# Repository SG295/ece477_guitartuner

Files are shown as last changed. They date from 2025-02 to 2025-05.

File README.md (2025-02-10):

# Automatic Guitar Tuner 🎸
☆ **Automatic Guitar Tuner Project for ECE477 (Senior Design) @ Purdue University** ☆

**Team Page: https://engineering.purdue.edu/477grp11/Team/team.html**

**Project Description:** Our automatic guitar tuner is a tool anyone can use by selecting the desired note and holding the tool against the tuning peg. A microphone will listen as the string is plucked by the user and make the proper adjustments thorugh a motor. An LCD screen will communicate when the guitar adjustments are finished being made. The design will also have other modes such as a free spin mode to allow the motor to assist in the restringing of a guitar.
Design parameters are:
  * A 3D printed case that holds all the components (PCB, battery, motor, etc.)
  * An STM32 microcontroller that controls all the components of the tuner (battery, motor, LCD screen, microphone)
  * A stepper motor connected to the microcontroller that rotates based on feedback from the microphone
  * A digital microphone that listens when prompted by the microcontroller. First, I2S is used to read the digital signal and then DSP is performed so that the microcontroller knows what frequency is being played.
  * A rechargable battery connected to a battery management system and the microcontroller. Powers all the components in the tuner.
  * A graphical LCD screen that is controlled by buttons on the tuner. It includes "Power", "^", ">", "<", and "v" buttons for the user to press to control the contents of the screen.

***

**For team members:**

Please make a branch for your respective part and title it according (i.e. if you're working on the motor, you can just title it "motor").

The command to create a branch (do this locally after you've pulled):
  * git checkout -b NEW_BRANCH_NAME

The commands (in order) to push your NEW branch: 
  * git add .
  * git commit -m "put message here"
  * git push origin -u NEW_BRANCH_NAME
   
**Once you have created and pushed the branch, you can push normally if you're on the branch. You can check this with "git branch".**

I have setup a platoform IO project here with basic settings with the STM32F407VG Discovery Boards we have at our table (looks like the image below). Make sure you're actually within the project folder (titled "PlatformIO-GuitarTuner") and not this repo when trying to upload code to the board. I'll list some documentation that will be useful below:
  * Reference Manual: https://www.st.com/resource/en/reference_manual/dm00031020-stm32f405-415-stm32f407-417-stm32f427-437-and-stm32f429-439-advanced-arm-based-32-bit-mcus-stmicroelectron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
  * STM32F407 Data Sheet: https://www.st.com/resource/en/datasheet/dm00037051.pdf

**DISCOVERY BOARD:**
71fB+DA9BdL _AC_UF894,1000_QL80_

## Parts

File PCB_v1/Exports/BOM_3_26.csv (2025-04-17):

Reference | Value | MFP | Qty | DNP | Packed?
C2 | 1uF |  | 1
C4 | 0.47uF |  | 1
C8 | 0.01uF |  | 1
C10 | 100uF | EEE1AA101WR | 1
C12 | 0.1uF |  | 1
C25 | 1uF | TAJA105K016RNJ | 1
F1 | C1F 2 | C1F 2 (CA0612KRX7R7BB104) | 1
F2 | MFU0805FF01000P500 | MFU0805FF01000P500 | 1
J3 | JST_B2B-PH-K-S | S2B-PH-K-SLFSN | 1
J6 | OLED Conn_02x04 | Genereic 2x4 2.56 mm | 1
J7 | B4B-XH-A | B4B-XH-A | 1
J8 | Conn_01x02_Pin |  | 1
J9 | Conn_02x05_Odd_Even |  | 1
J10 | Conn_01x03 | Genereic 3 pin 2.56mm | 1
J11 | 1051640001 | 1051640001 | 1
R8 | 0.01 1% | WSL0805R0100FEA1 | 1
R12 | 1.1k |  | 1
R13 | 47k |  | 1
R14 | 1.5k |  | 1
R23 | 10k |  | 1 | DNP
R24 | 47k |  | 1 | DNP
RN1 | 1k | EXB-2HV102JV | 1
RN2 | 10k | EXB-2HV103JV | 1
RN3 | 680 | EXB-38V681JV | 1
RV1 | 10k | TRIM_TC33X-2-103E | 1
SW1 | SW_SPST | JST_B2B-PH-K-S | 1
SW8 | SW_Push | TS04-66-65-BK-160-SMT | 1
SW9 | SW_SPDT | PCM12SMTR | 1
U1 | BQ25185DLHR | BQ25185DLHR | 1
U2 | BQ27441-G1 | BQ27441-G1 | 1
U5 | DRV8834PWP | DRV8834PWP | 1
U6 | MAX7375AXR805 |  | 1
U7 | STM32F405RGTx | STM32F405RGT6 | 1
U8 | ESD9B5.0ST5G | ESD9B5.0ST5G | 1
C6,C7 | 100nF | CA0612KRX7R7BB104 | 2
C11,C17 | 10uF |  | 2
D1,D7 | Orange |  | 2
D9,D10 | Blue |  | 2
J1,J2 | B6B-PH-K-S | B6B-PH-K-S | 2
J4,J5 | Conn_01x05_Pin | Genereic 5 pin 2.56mm | 2
R5,R21 | 1k |  | 2
R15,R16 | 51k |  | 2
R18,R19 | 0.1 | WSTM0805QLR100FNR | 2
U3,U4 | SMS05T1G | SMS05T1G | 2
C1,C3,C5 | 22uF |  | 3
C9,C21,C23 | 2.2uF |  | 3
D2,D3,D6 | Green |  | 3
D4,D5,D8 | Red |  | 3
R6,R7,R11 | 5.1k |  | 3
R1,R2,R3,R4 | 680 |  | 4
TP3,TP4,TP5,TP6 | TestPoint | N/A | 4
R9,R10,R17,R20,R22 | 10k |  | 5
SW2,SW3,SW4,SW5,SW6,SW7 | SW_Push | JST_B2B-PH-K-S | 6
C15,C16,C18,C19,C20,C22,C24 | 100nF |  | 7
TP1,TP8,TP9,TP10,TP11,TP12,TP13 | ~ | N/A | 7

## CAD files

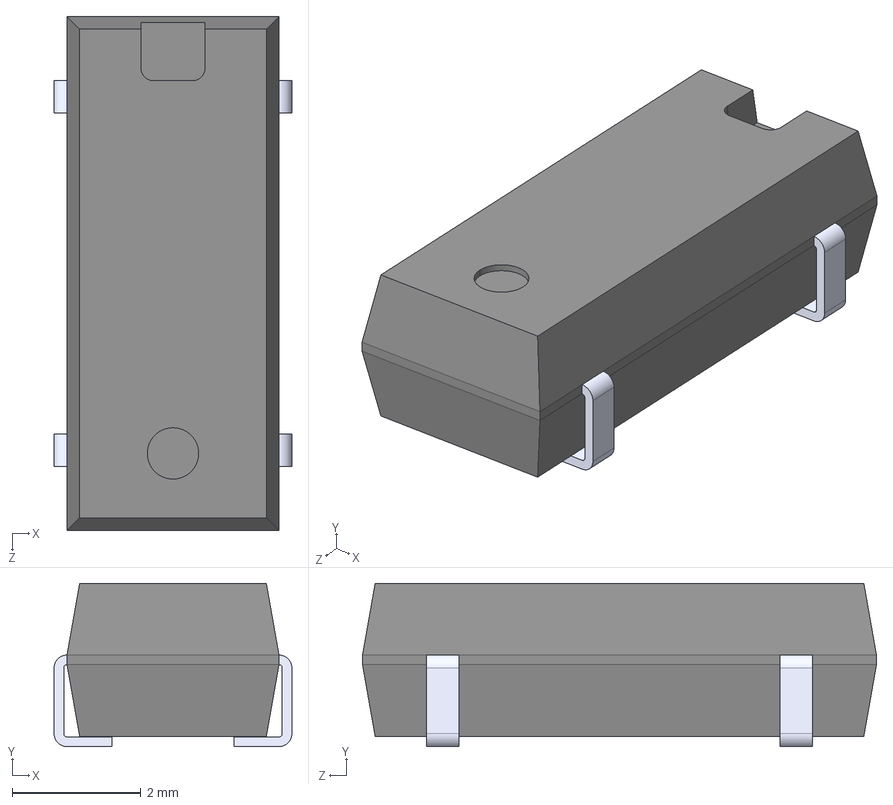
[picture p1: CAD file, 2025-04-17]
Parts_Library/MC-306_32.7680K-A5__ROHS.step
3.70 x 2.54 x 8.00 mm

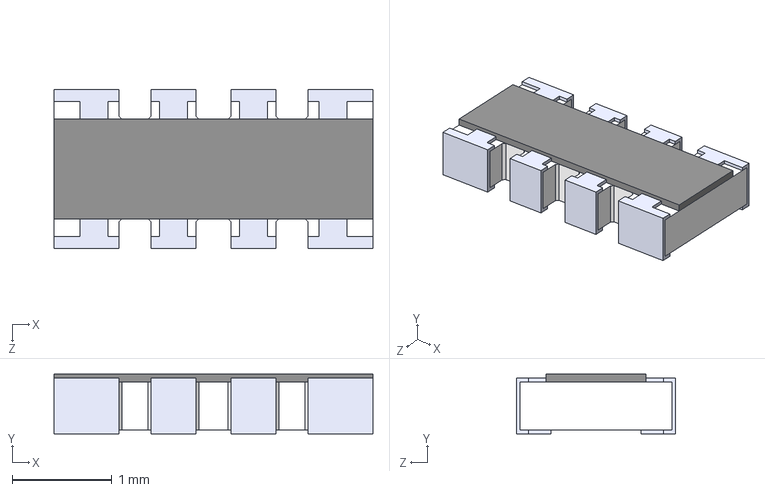
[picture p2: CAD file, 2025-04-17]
Parts_Library/EXB-38V681JV.step
3.20 x 0.6 x 1.60 mm

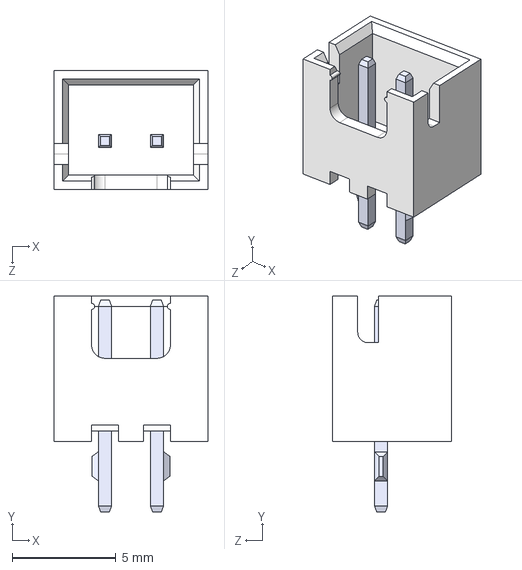
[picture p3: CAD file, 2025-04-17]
Parts_Library/B2B-XH-A.step
7.40 x 10.4 x 5.75 mm

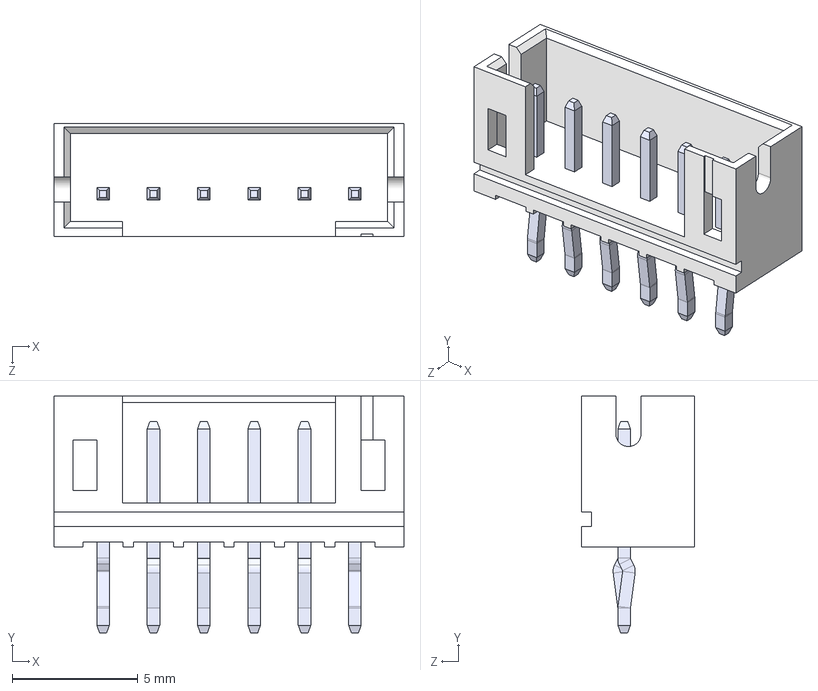
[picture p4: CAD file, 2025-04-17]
Parts_Library/B6B-PH-K-S.step
13.9 x 9.40 x 4.50 mm
pin x 6

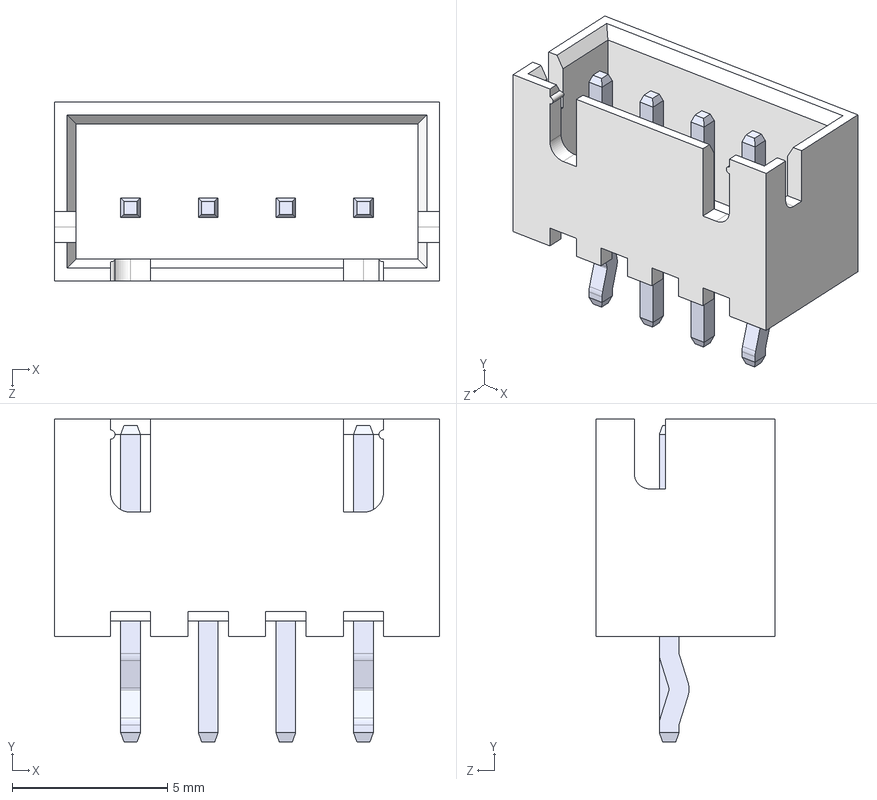
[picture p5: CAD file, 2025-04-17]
Parts_Library/B4B-XH-A.step
12.4 x 10.4 x 5.75 mm

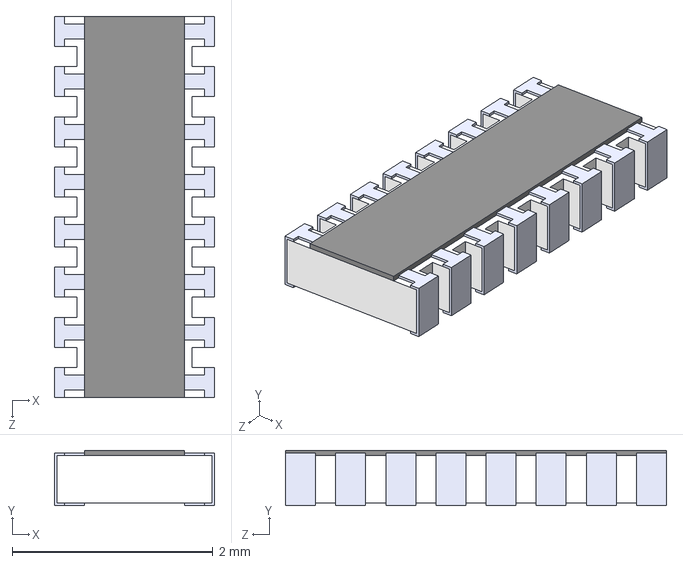
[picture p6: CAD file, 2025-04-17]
Parts_Library/EXB-2HV102JV.step
1.60 x 0.55 x 3.80 mm

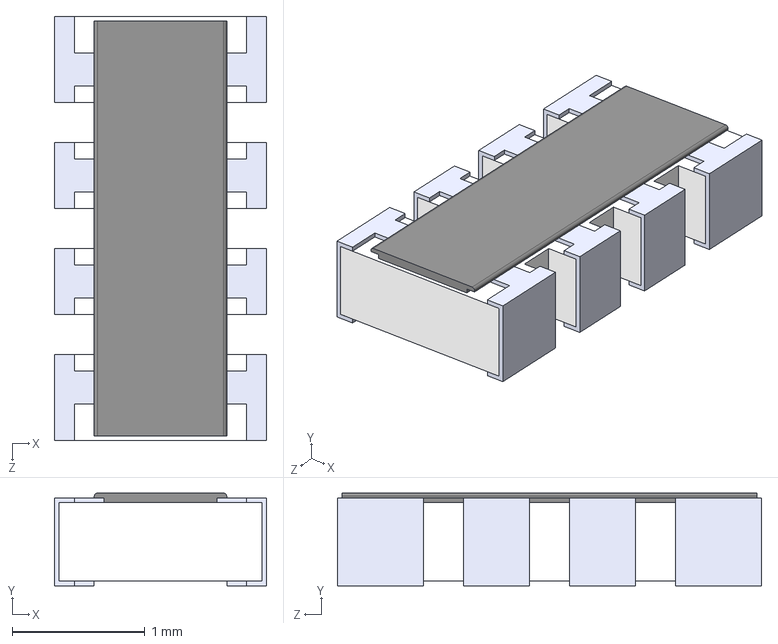
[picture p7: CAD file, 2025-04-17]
Parts_Library/YC164-JR-0722RL.step
1.60 x 0.7 x 3.20 mm

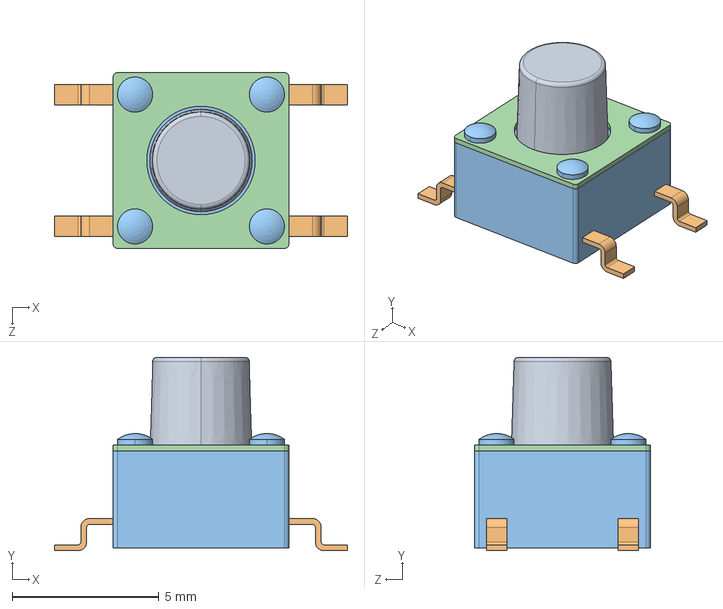
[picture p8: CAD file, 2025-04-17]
Parts_Library/TS04-66-65-BK-160-SMT.step
10.0 x 6.60 x 6.00 mm

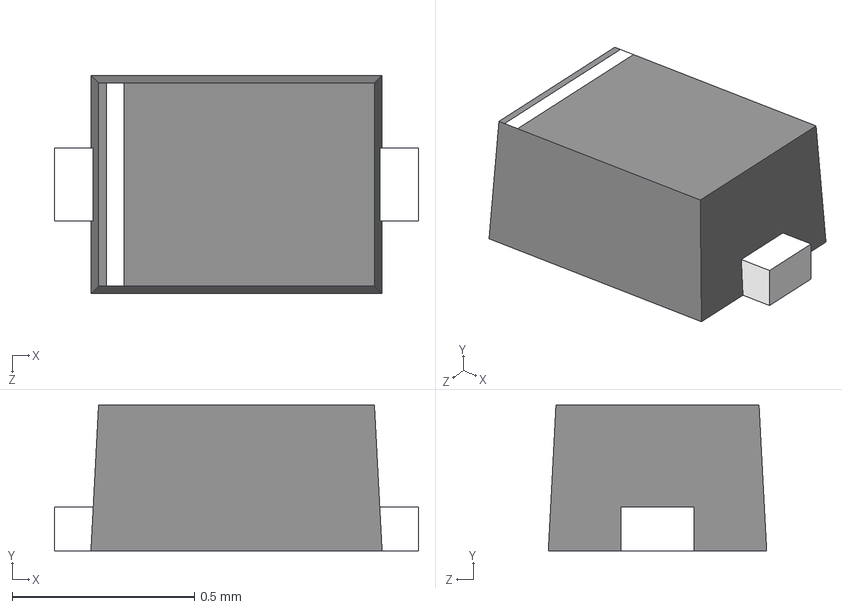
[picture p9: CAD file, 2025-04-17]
Parts_Library/ESD9B5.0ST5G.step
1 x 0.4 x 0.6 mm

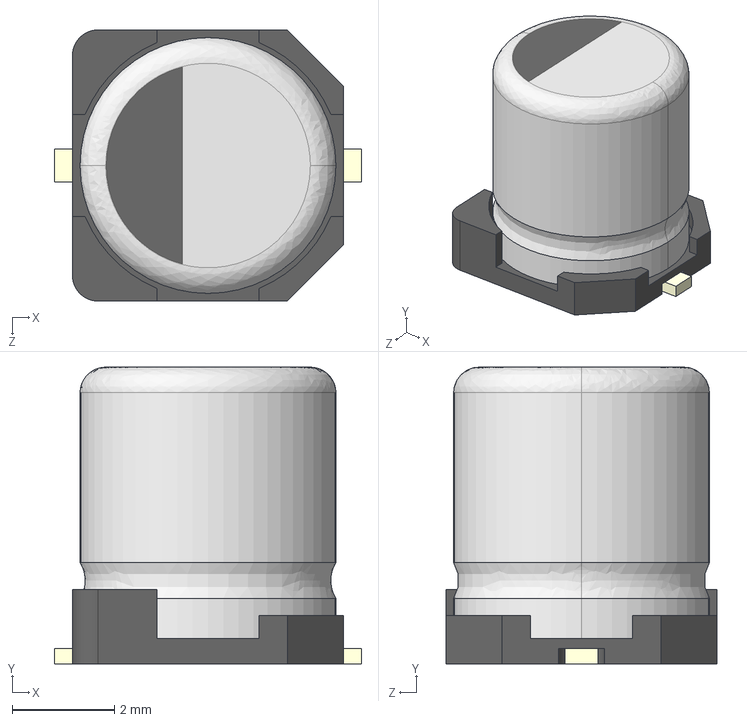
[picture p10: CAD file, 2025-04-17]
Parts_Library/EEE1AA101WR.step
6.00 x 5.80 x 5.30 mm

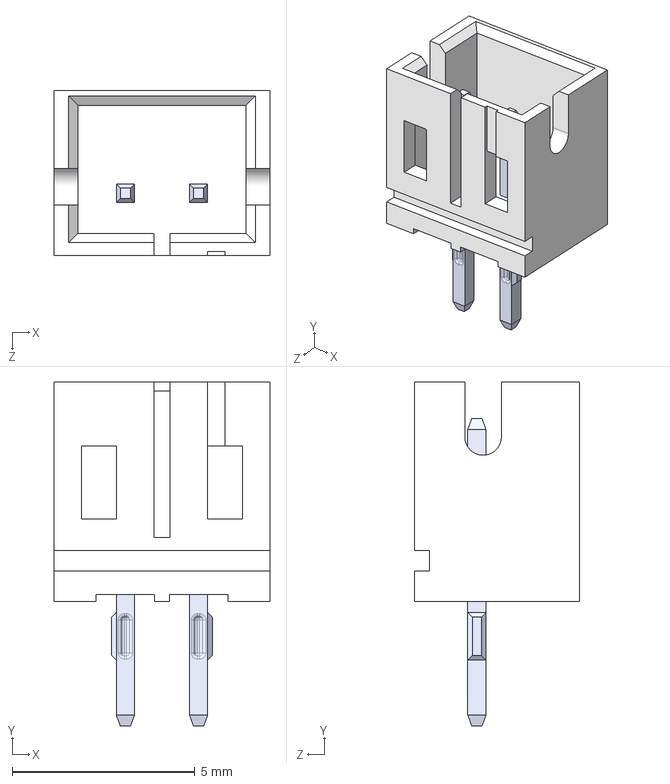
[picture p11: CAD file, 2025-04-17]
Parts_Library/B2B-PH-K-S.step
5.90 x 9.40 x 4.50 mm

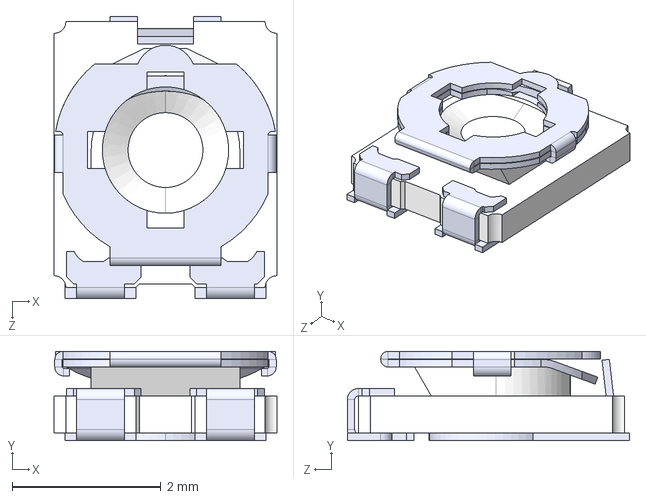
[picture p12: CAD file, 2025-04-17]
Parts_Library/TC33X-2-103E.step
3.00 x 1.20 x 3.80 mm

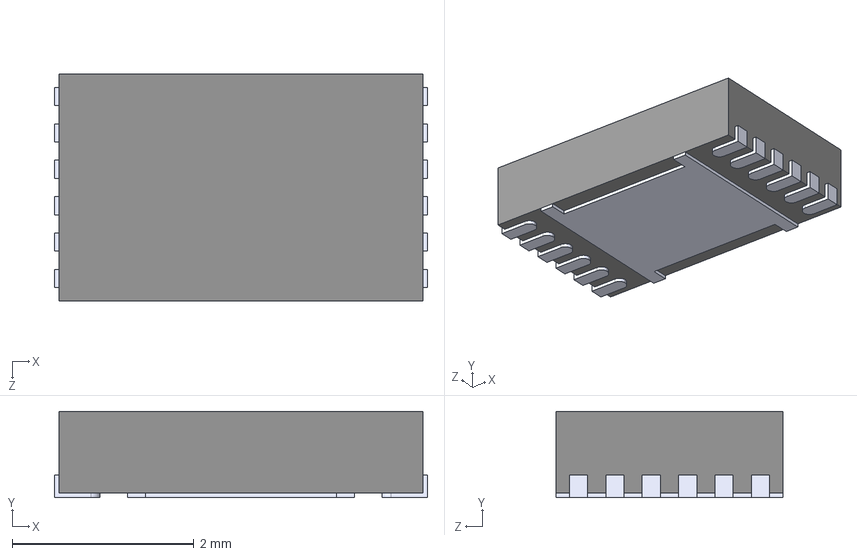
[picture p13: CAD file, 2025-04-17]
Parts_Library/BQ27441DRZT-G1A.step
4.10 x 0.95 x 2.50 mm

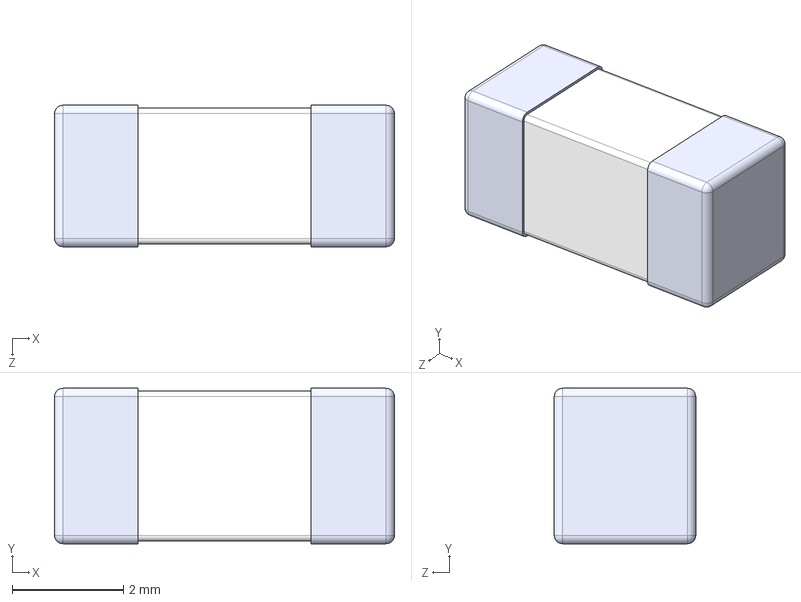
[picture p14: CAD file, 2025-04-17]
Parts_Library/0679L2000-05.step
6.10 x 2.79 x 2.54 mm

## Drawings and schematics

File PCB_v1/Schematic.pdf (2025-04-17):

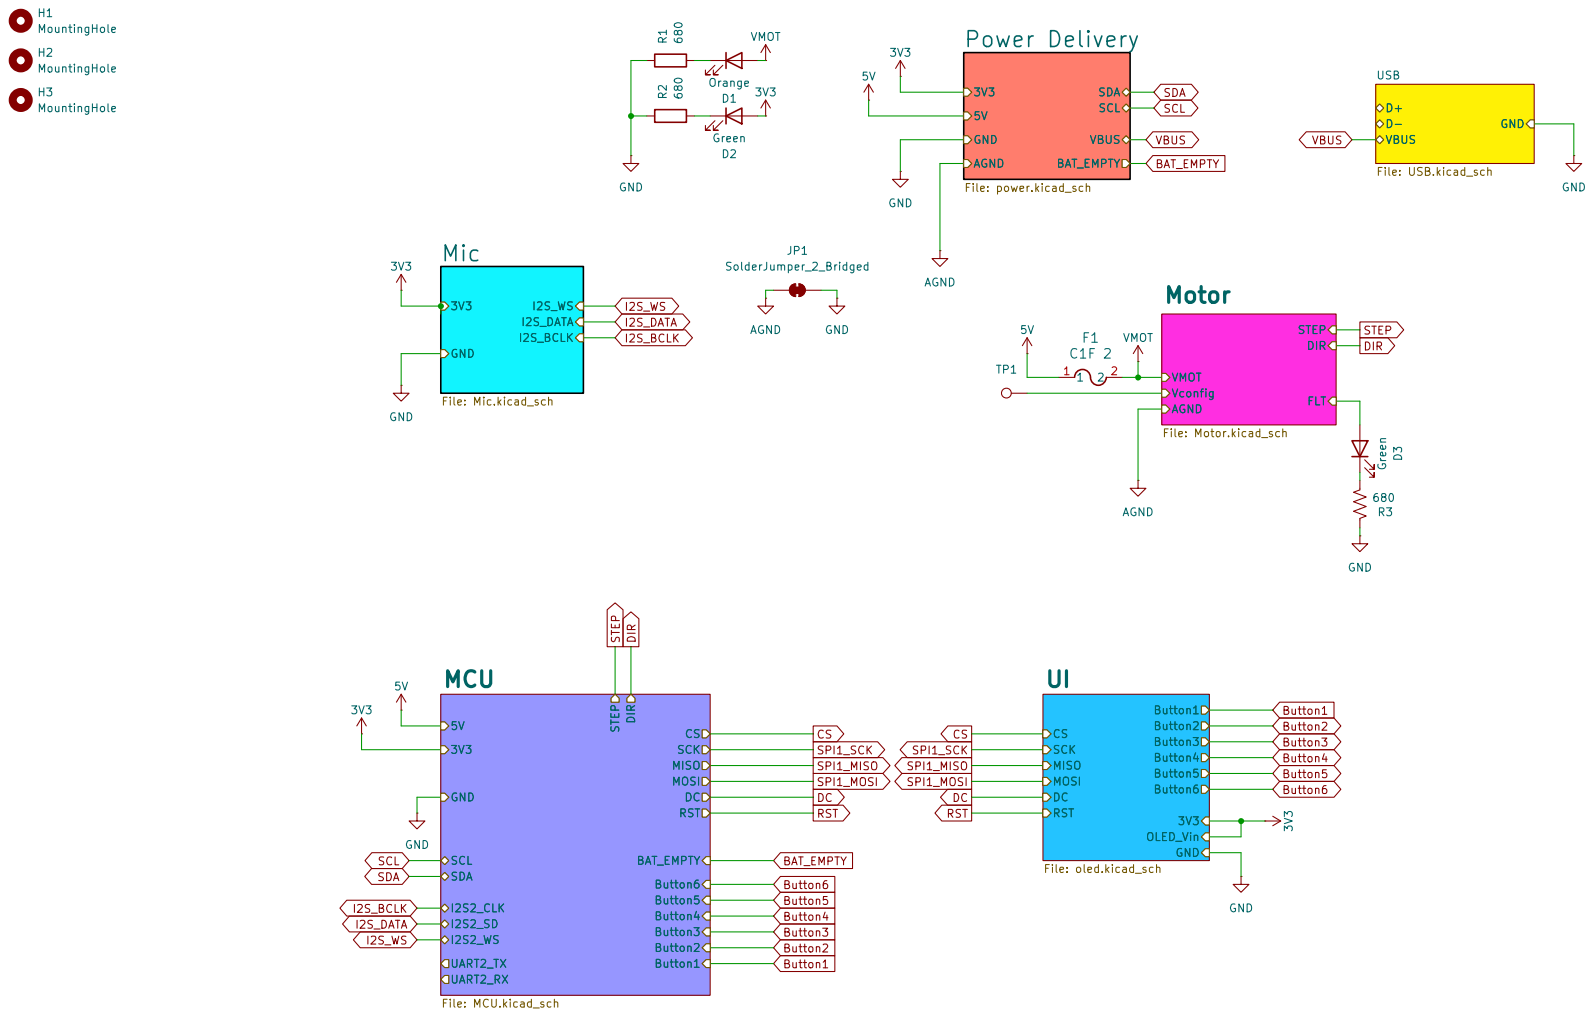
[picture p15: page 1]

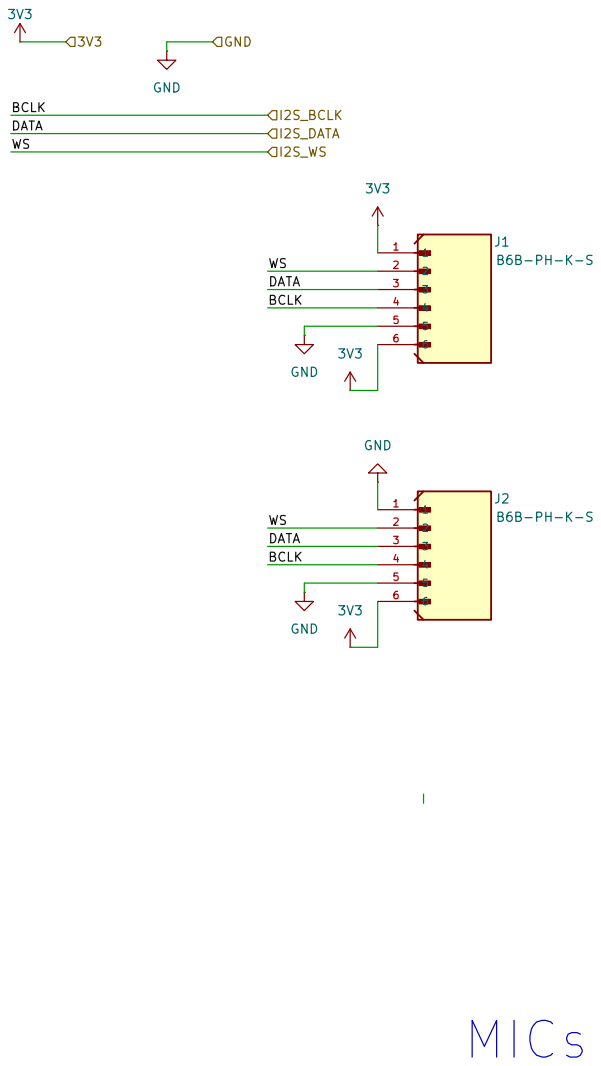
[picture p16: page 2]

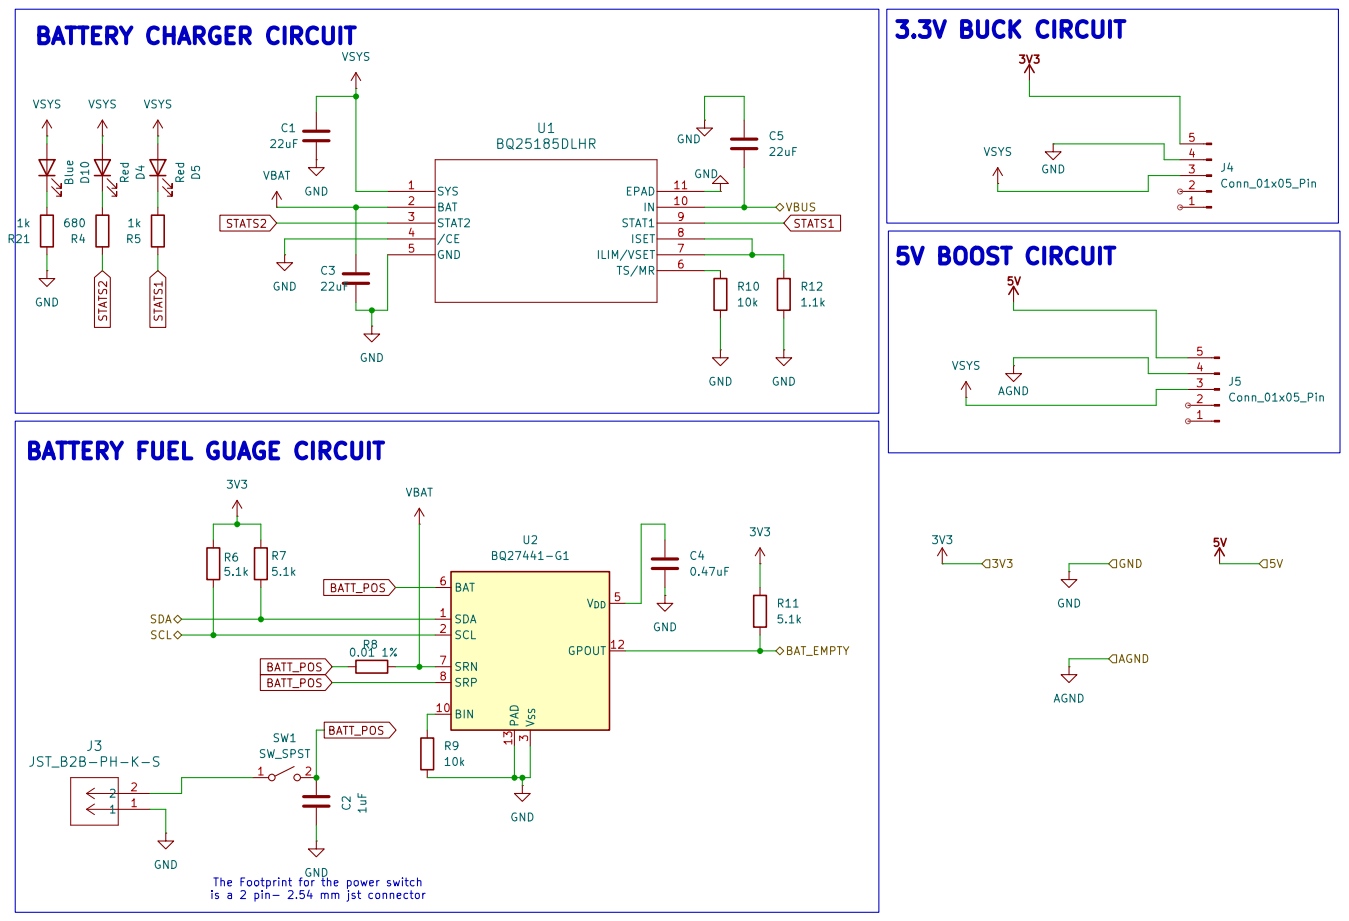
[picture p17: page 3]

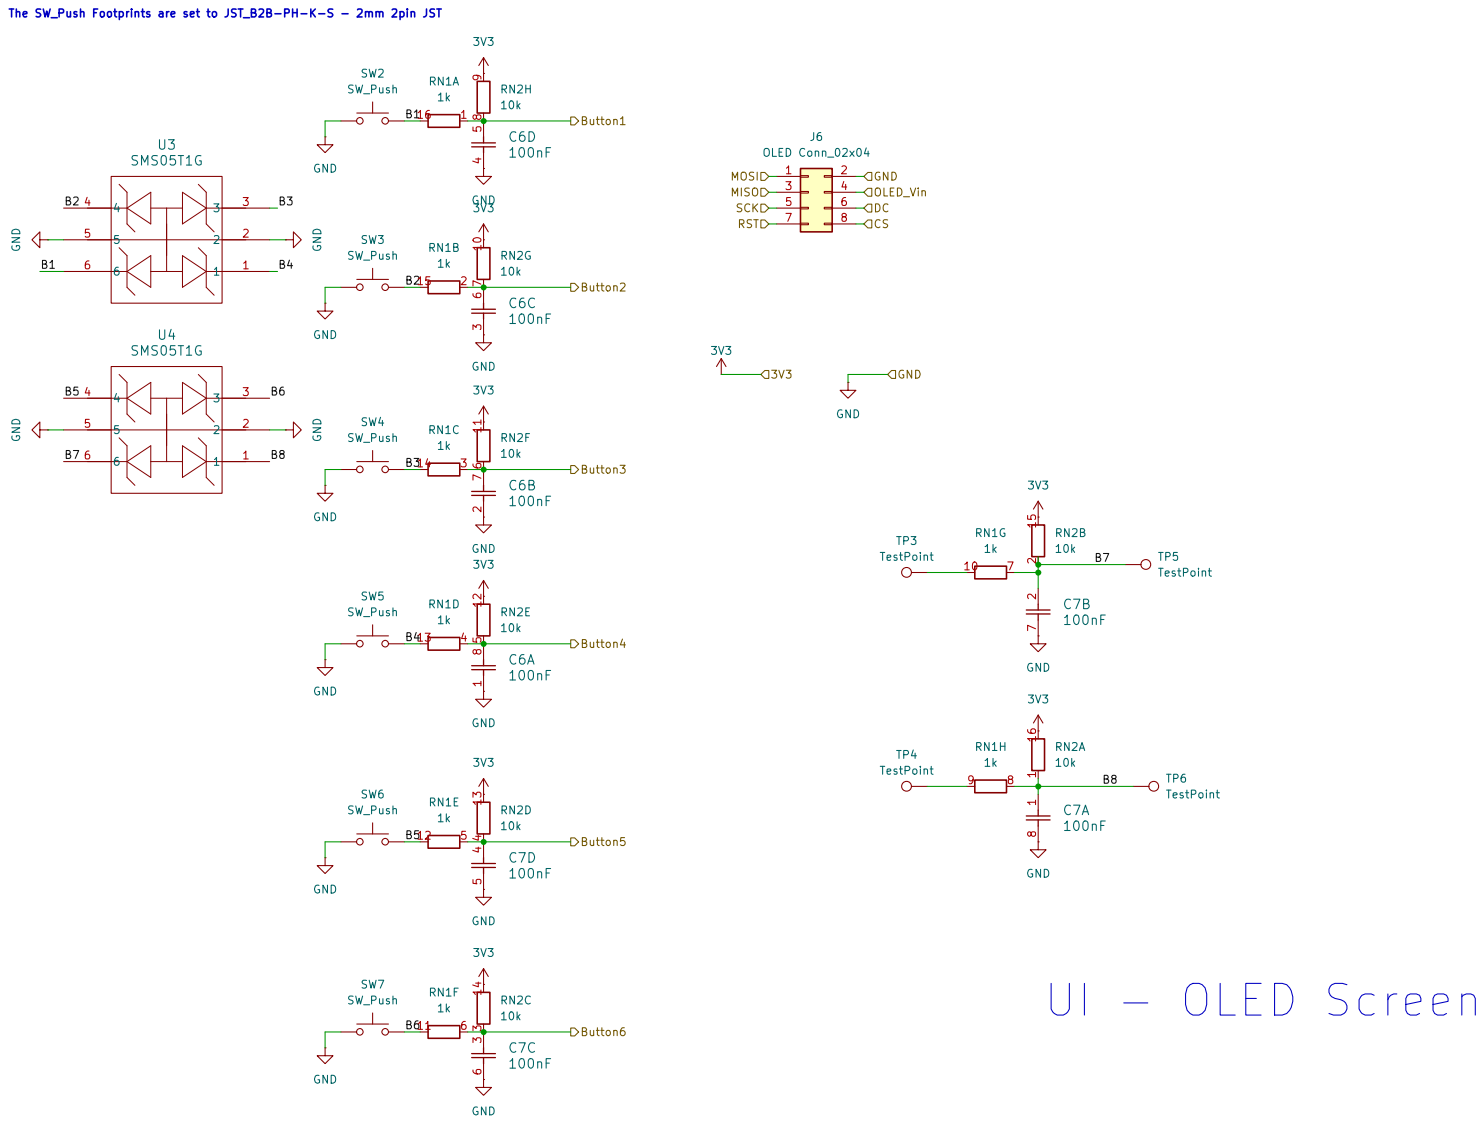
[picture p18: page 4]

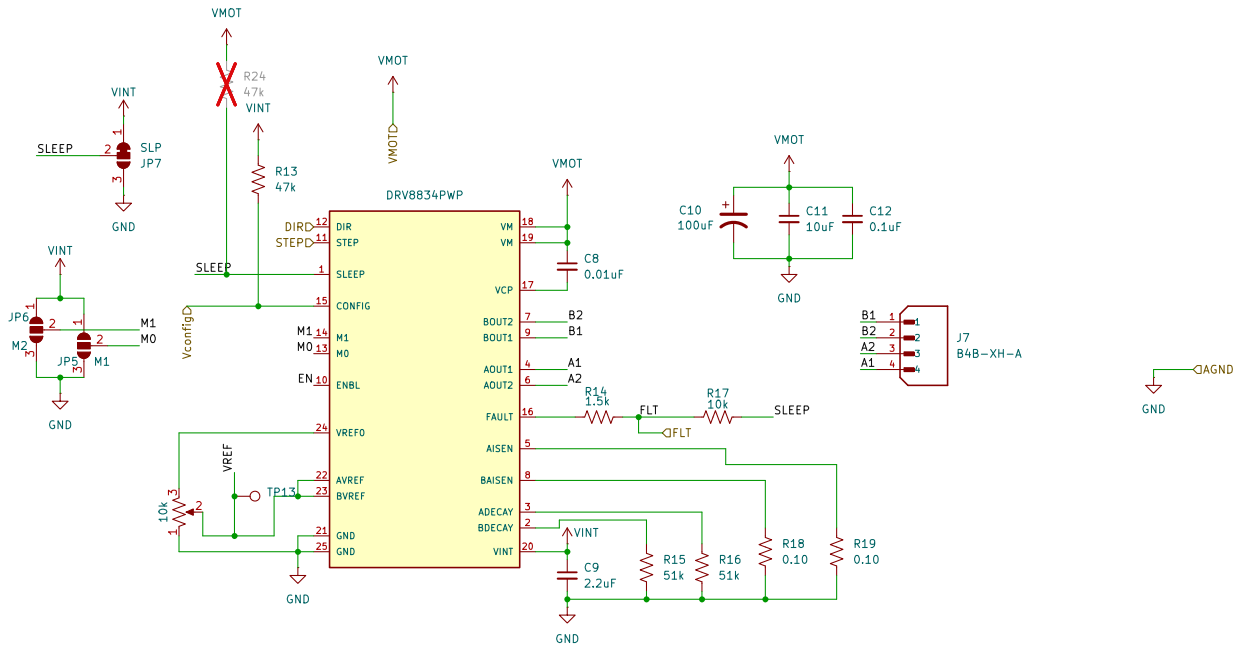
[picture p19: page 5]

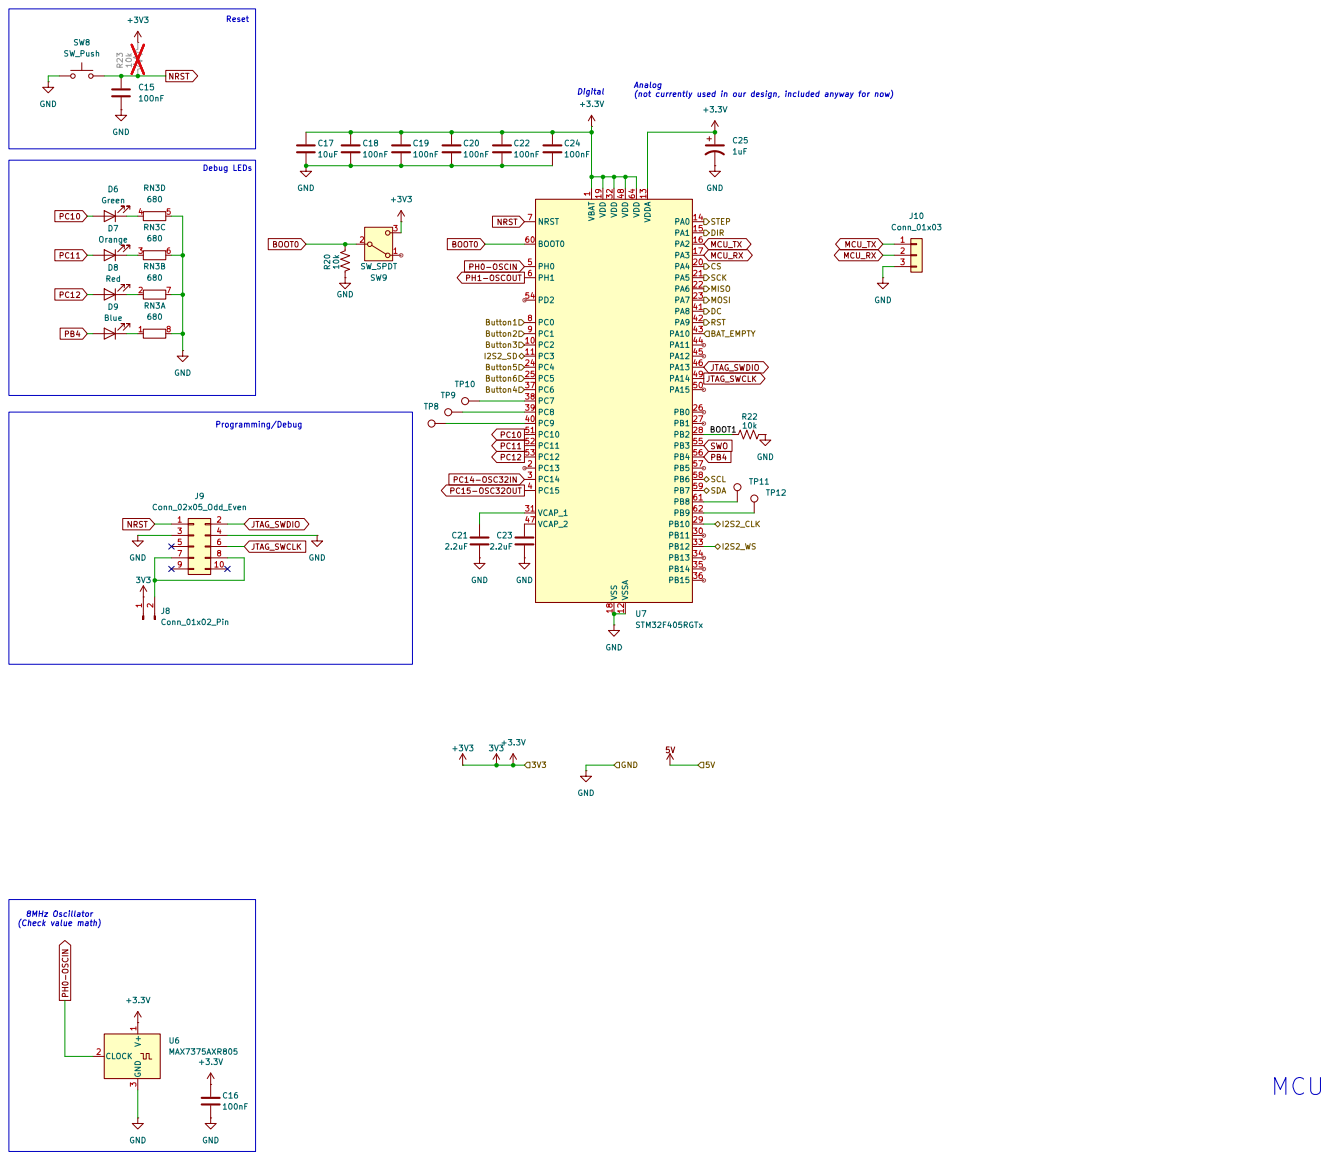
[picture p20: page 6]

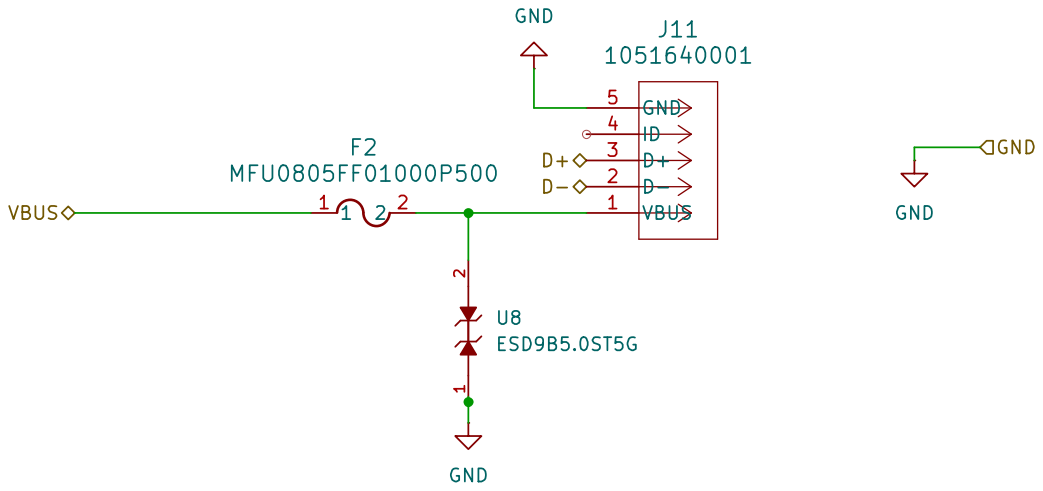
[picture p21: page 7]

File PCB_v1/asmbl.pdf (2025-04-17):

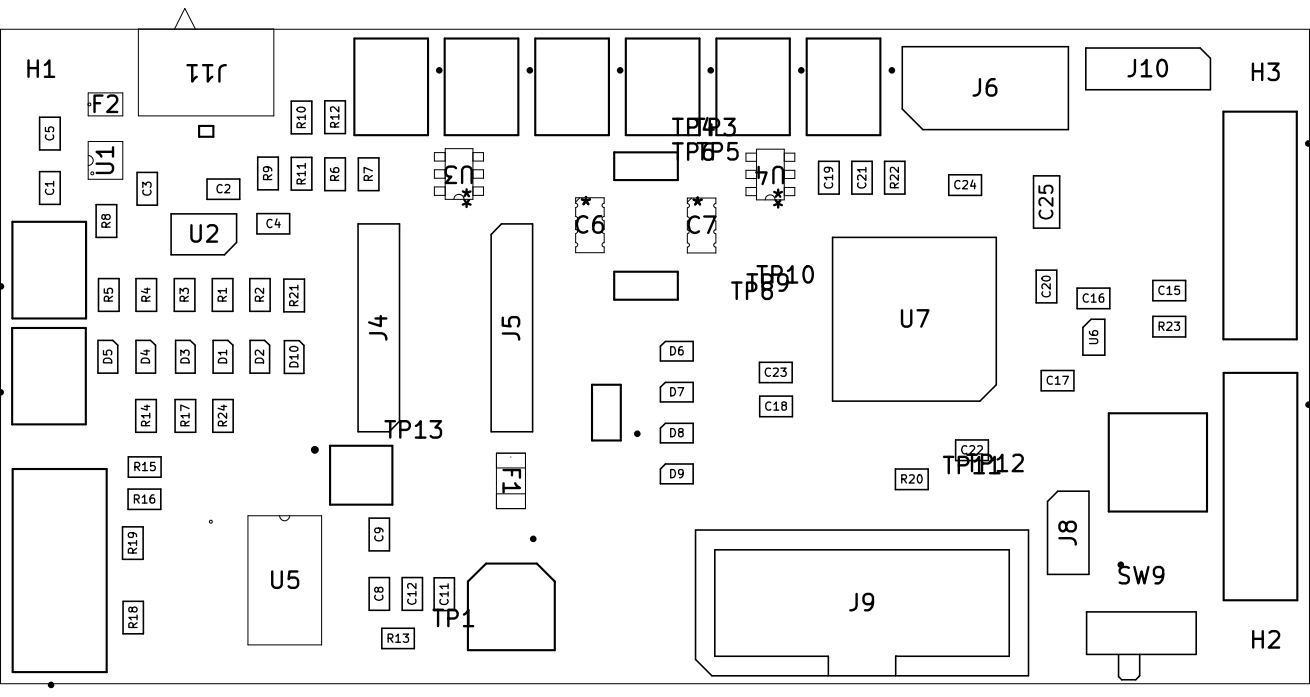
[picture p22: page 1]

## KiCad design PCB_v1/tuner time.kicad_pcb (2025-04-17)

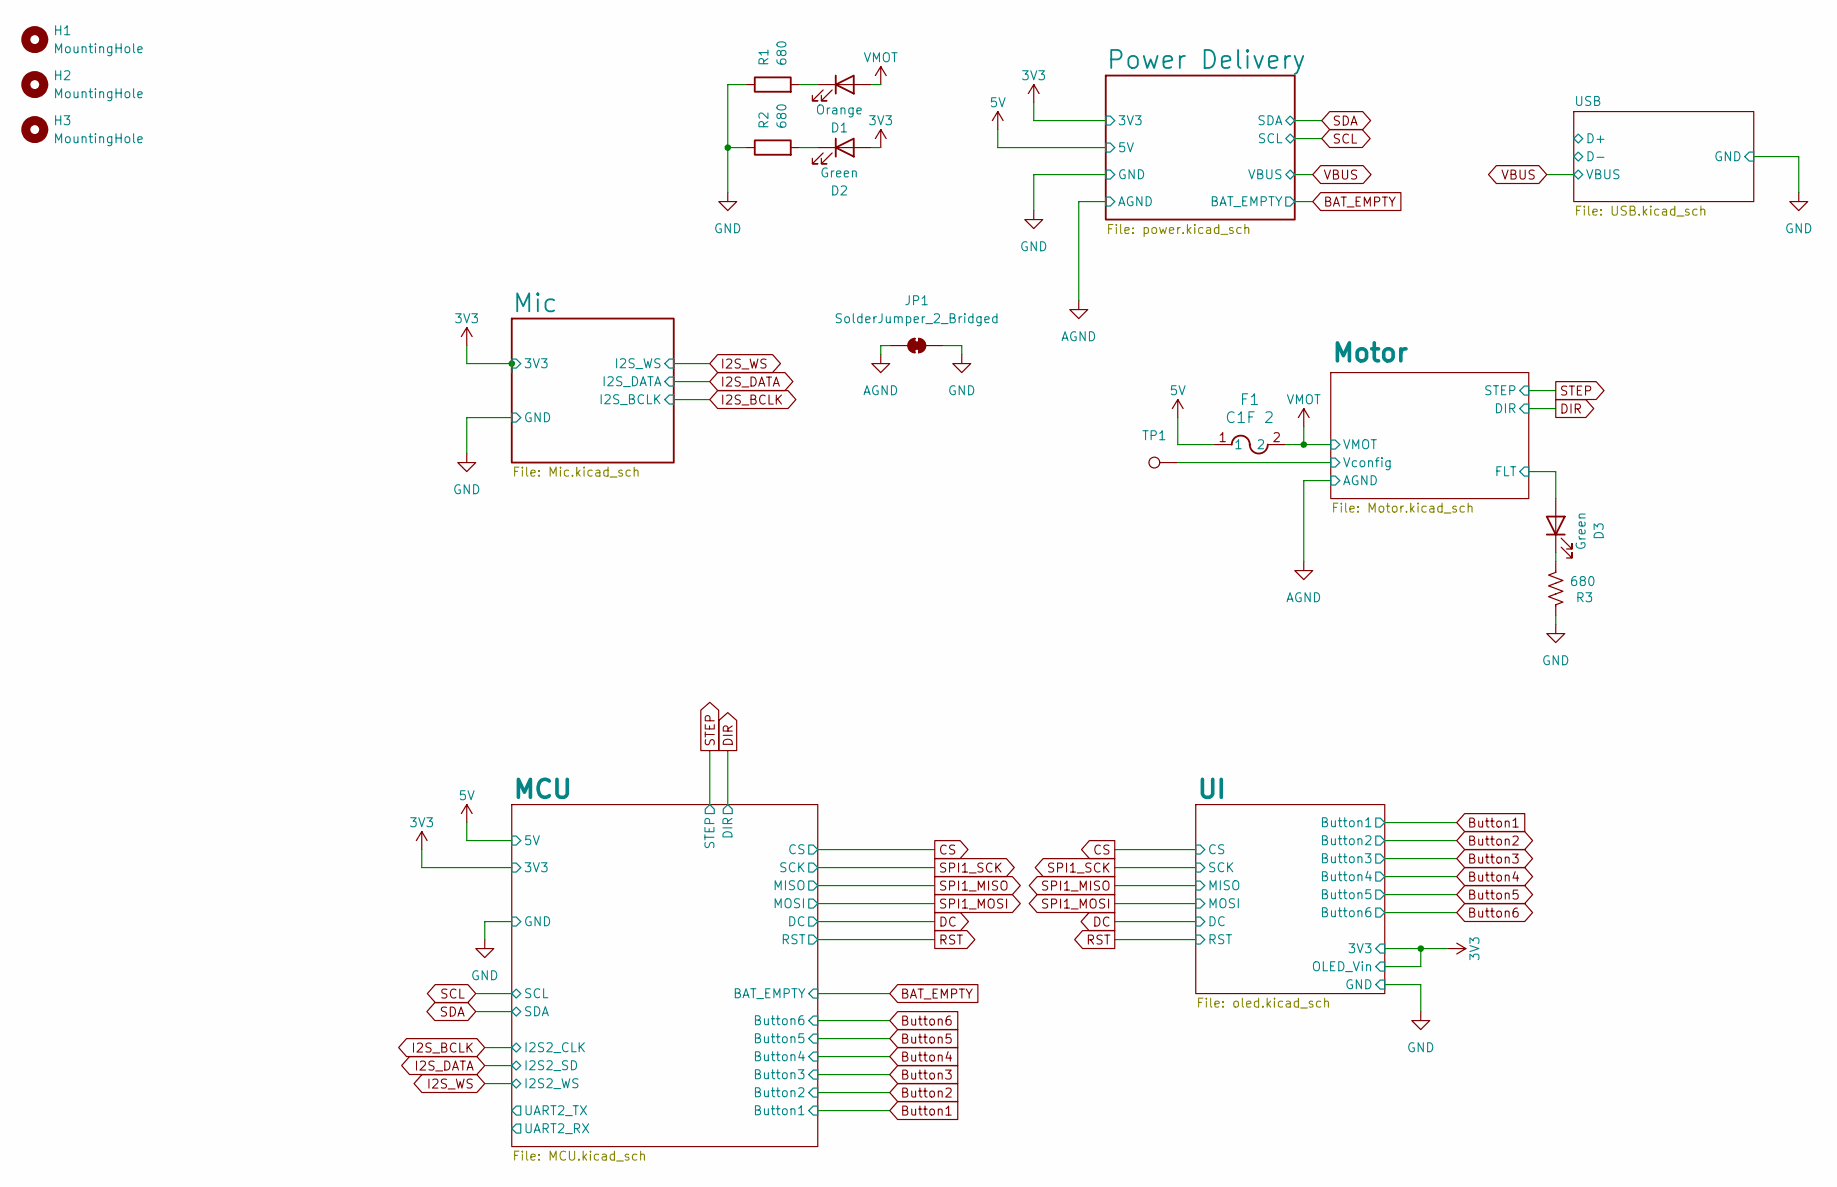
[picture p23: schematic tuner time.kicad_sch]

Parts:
D1: Orange; LED_0805_2012Metric_Pad1.15x1.40mm_HandSolder
D2, D3: Green; LED_0805_2012Metric_Pad1.15x1.40mm_HandSolder
F1: C1F 2; C1_BEL
H1, H2, H3: MountingHole; MountingHole_2.2mm_M2_DIN965_Pad_TopOnly
JP1: SolderJumper_2_Bridged; SolderJumper-2_P1.3mm_Bridged2Bar_RoundedPad1.0x1.5mm
R1, R2, R3: 680; R_0805_2012Metric
TP1: TestPoint_THTPad_D0.8mm_Drill0.4mm

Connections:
3V3: D2.2 (A); also elsewhere on the board
5V: F1.1; also elsewhere on the board
/Motor/FLT: D3.2 (A); also elsewhere on the board
/Motor/Vconfig: TP1.1; also elsewhere on the board
AGND: JP1.1 (A); also elsewhere on the board
GND: JP1.2 (B), R1.1, R2.1, R3.2; also elsewhere on the board
unnamed: D1.1 (K), R1.2
unnamed: D2.1 (K), R2.2
unnamed: D3.1 (K), R3.1
VMOT: D1.2 (A), F1.2; also elsewhere on the board

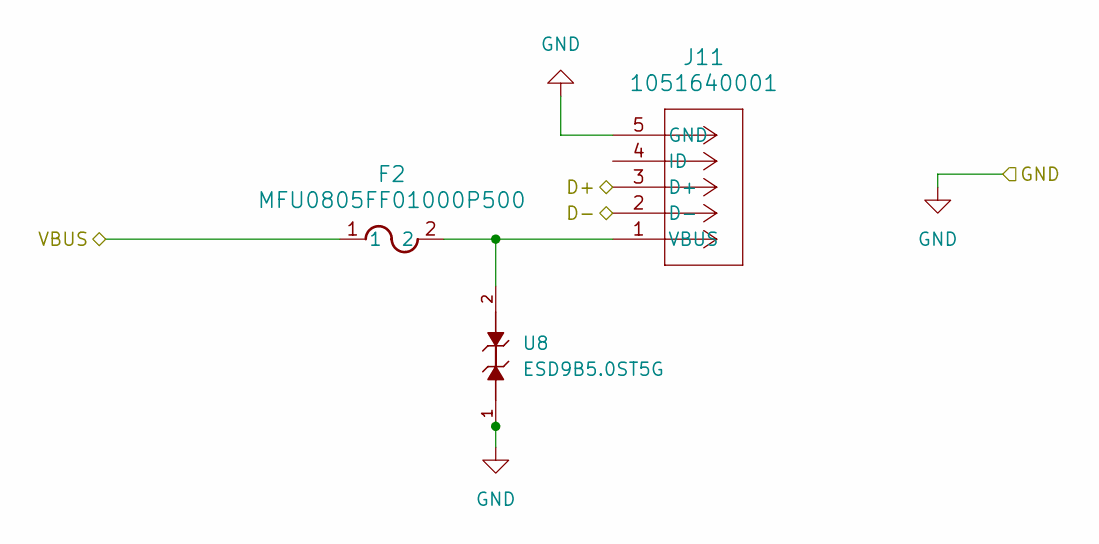
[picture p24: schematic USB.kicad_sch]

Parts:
F2: MFU0805FF01000P500; FUS_VISHAY_MFU0805_VIS
J11: 1051640001; CON00906_5_MOL
U8: ESD9B5.0ST5G; SODFL1006X40N

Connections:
GND: J11.5 (GND), U8.1; also elsewhere on the board
unnamed: F2.2, J11.1 (VBUS), U8.2
VBUS: F2.1; also elsewhere on the board

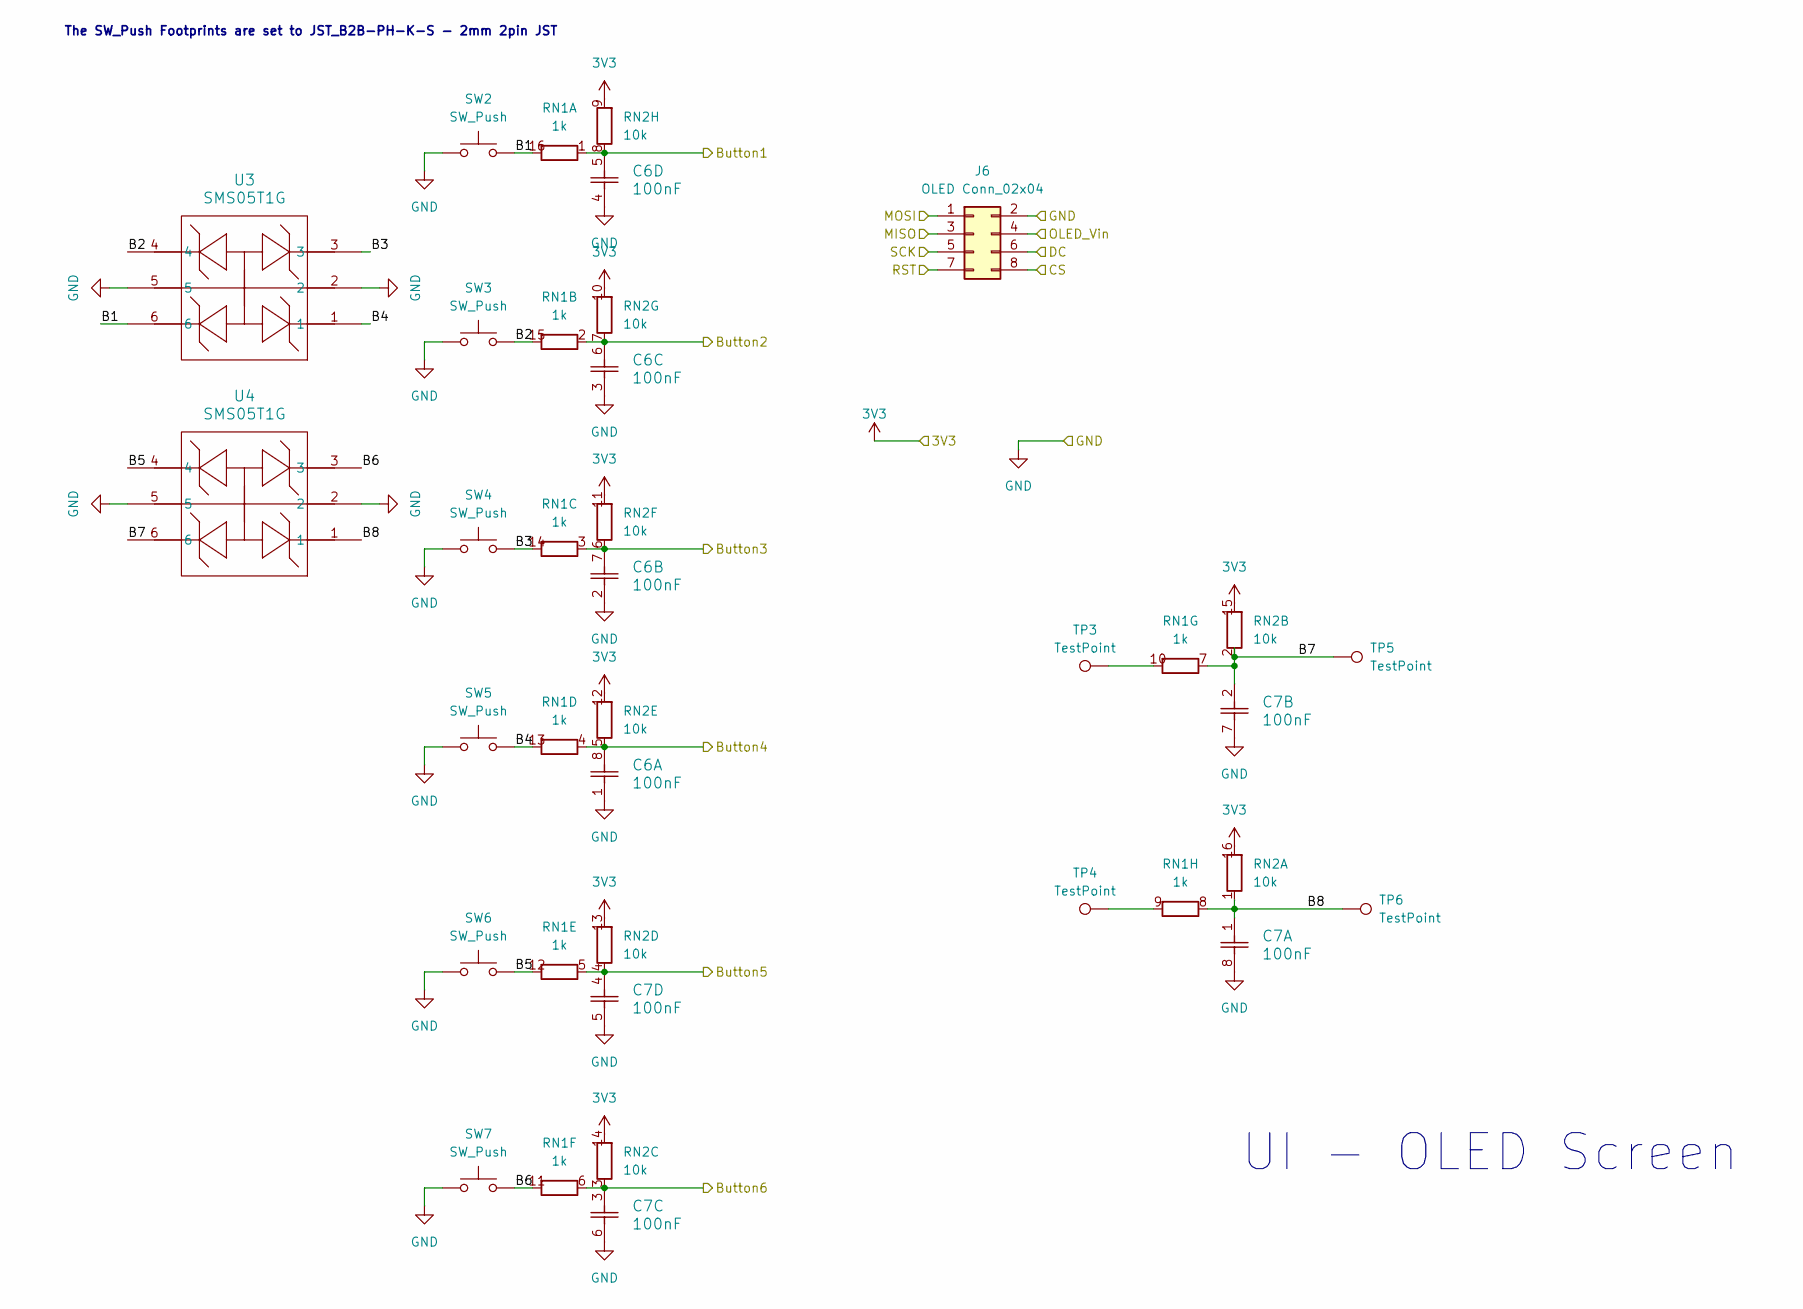
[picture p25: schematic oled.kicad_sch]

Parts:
C6, C7: 100nF; CAP_CA0612_3P2X1P6_YAG
J6: OLED Conn_02x04; PinHeader_2x04_P2.54mm_Vertical
RN1: 1k; RESCAXE50P280X160X55-16N
RN2: 10k; RESCAXE50P280X160X55-16N
SW2, SW3, SW4, SW5, SW6, SW7: SW_Push; JST_B2B-PH-K-S
TP3, TP4, TP5, TP6: TestPoint; TestPoint_THTPad_D0.8mm_Drill0.4mm
U3, U4: SMS05T1G; SOIC_05T1G_ONS

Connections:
3V3: J6.4, RN2.9 (R8.2), RN2.10 (R7.2), RN2.11 (R6.2), RN2.12 (R5.2), RN2.13 (R4.2), RN2.14 (R3.2), RN2.15 (R2.2), RN2.16 (R1.2); also elsewhere on the board
/UI/B1: RN1.16 (R1.2), SW2.2, U3.6
/UI/B2: RN1.15 (R2.2), SW3.2, U3.4
/UI/B3: RN1.14 (R3.2), SW4.2, U3.3
/UI/B4: RN1.13 (R4.2), SW5.2, U3.1
/UI/B5: RN1.12 (R5.2), SW6.2, U4.4
/UI/B6: RN1.11 (R6.2), SW7.2, U4.3
/UI/B7: C7.2, RN1.7 (R7.1), RN2.2 (R2.1), TP5.1, U4.6
/UI/B8: C7.1, RN1.8 (R8.1), RN2.1 (R1.1), TP6.1, U4.1
Button1: C6.5, RN1.1 (R1.1), RN2.8 (R8.1); also elsewhere on the board
Button2: C6.6, RN1.2 (R2.1), RN2.7 (R7.1); also elsewhere on the board
Button3: C6.7, RN1.3 (R3.1), RN2.6 (R6.1); also elsewhere on the board
Button4: C6.8, RN1.4 (R4.1), RN2.5 (R5.1); also elsewhere on the board
Button5: C7.4, RN1.5 (R5.1), RN2.4 (R4.1); also elsewhere on the board
Button6: C7.3, RN1.6 (R6.1), RN2.3 (R3.1); also elsewhere on the board
CS: J6.8; also elsewhere on the board
DC: J6.6; also elsewhere on the board
GND: C6.1, C6.2, C6.3, C6.4, C7.5, C7.6, C7.7, C7.8, J6.2, SW2.1, SW3.1, SW4.1, SW5.1, SW6.1, SW7.1, U3.2, U3.5, U4.2, U4.5; also elsewhere on the board
unnamed: RN1.10 (R7.2), TP3.1
unnamed: RN1.9 (R8.2), TP4.1
RST: J6.7; also elsewhere on the board
SPI1_MISO: J6.3; also elsewhere on the board
SPI1_MOSI: J6.1; also elsewhere on the board
SPI1_SCK: J6.5; also elsewhere on the board

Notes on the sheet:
The SW_Push Footprints are set to JST_B2B-PH-K-S - 2mm 2pin JST
UI - OLED Screen

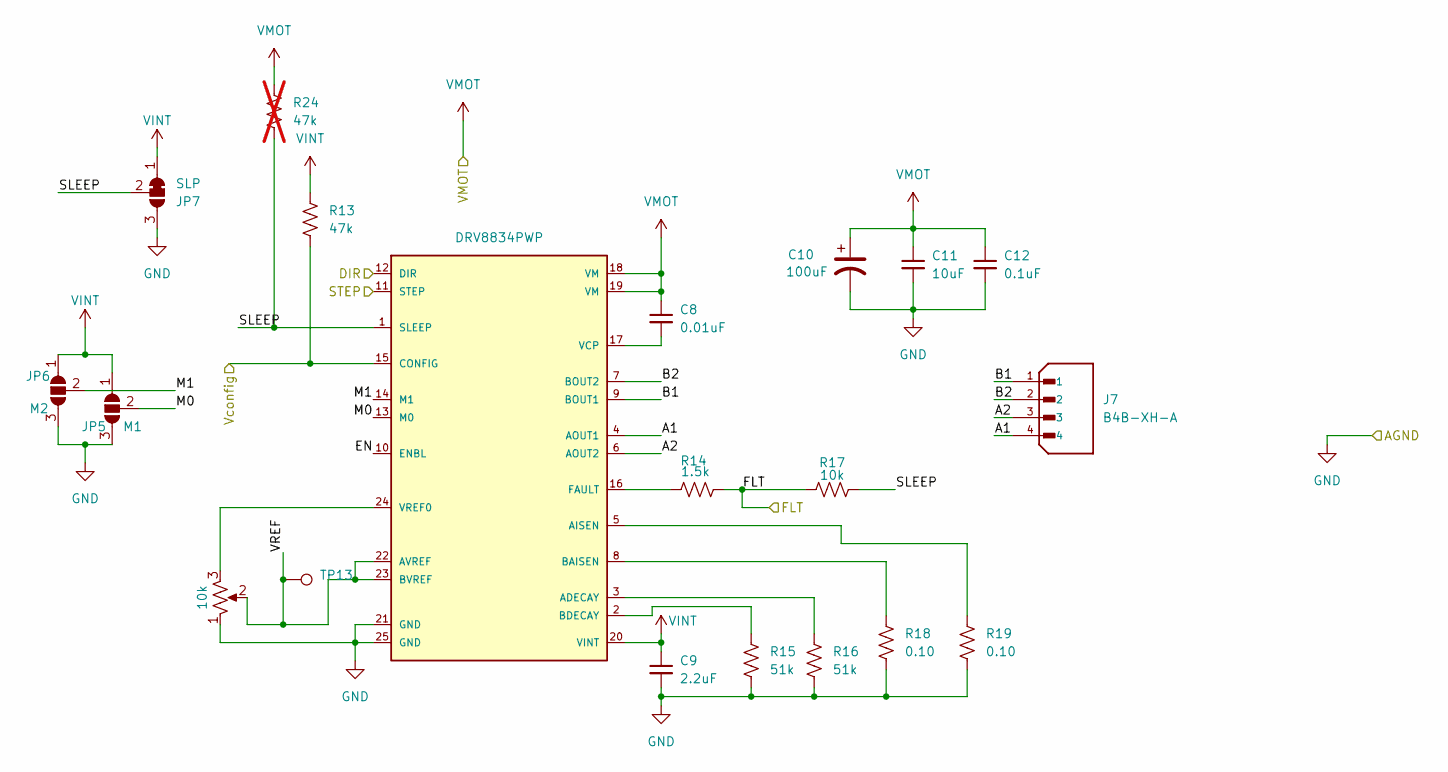
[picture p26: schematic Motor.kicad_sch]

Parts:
C8: 0.01uF; C_0805_2012Metric
C9: 2.2uF; C_0805_2012Metric
C10: 100uF; CAP_EEE1AA101WR
C11: 10uF; C_0805_2012Metric
C12: 0.1uF; C_0805_2012Metric
J7: B4B-XH-A; JST_B4B-XH-A; PARTREV 7/4/21
JP5: M1; SolderJumper-3_P1.3mm_Open_RoundedPad1.0x1.5mm
JP6: M2; SolderJumper-3_P1.3mm_Open_RoundedPad1.0x1.5mm
JP7: SLP; SolderJumper-3_P1.3mm_Bridged12_RoundedPad1.0x1.5mm
R13: 47k; R_0805_2012Metric
R14: 1.5k; R_0805_2012Metric
R15, R16: 51k; R_0805_2012Metric
R17: 10k; R_0805_2012Metric
R18, R19: 0.10; R_0805_2012Metric
R24: 47k; R_0805_2012Metric; not fitted
RV1: 10k; TRIM_TC33X-2-103E
TP13: TestPoint_THTPad_D0.8mm_Drill0.4mm
U5: DRV8834PWP; SOP65P640X120-25N

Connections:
/Motor/A1: J7.4, U5.4 (AOUT1)
/Motor/A2: J7.3, U5.6 (AOUT2)
/Motor/B1: J7.1, U5.9 (BOUT1)
/Motor/B2: J7.2, U5.7 (BOUT2)
/Motor/EN: U5.10 (ENBL)
/Motor/FLT: R14.2, R17.1; also elsewhere on the board
/Motor/M0: JP5.2 (C), U5.13 (M0)
/Motor/M1: JP6.2 (C), U5.14 (M1)
/Motor/SLEEP: JP7.2 (C), R17.2, R24.2, U5.1 (SLEEP)
/Motor/VREF: RV1.2, TP13.1, U5.22 (AVREF), U5.23 (BVREF)
/Motor/Vconfig: R13.2, U5.15 (CONFIG); also elsewhere on the board
AGND: C9.2, C10.2, C11.2, C12.2, JP5.3 (B), JP6.3 (B), JP7.3 (B), R15.2, R16.2, R18.2, R19.2, RV1.1, U5.21 (GND), U5.25 (GND); also elsewhere on the board
DIR: U5.12 (DIR); also elsewhere on the board
unnamed: R16.1, U5.3 (ADECAY)
unnamed: R19.1, U5.5 (AISEN)
unnamed: R18.1, U5.8 (BAISEN)
unnamed: R15.1, U5.2 (BDECAY)
unnamed: R14.1, U5.16 (FAULT)
unnamed: C8.2, U5.17 (VCP)
unnamed: RV1.3, U5.24 (VREF0)
STEP: U5.11 (STEP); also elsewhere on the board
VINT: C9.1, JP5.1 (A), JP6.1 (A), JP7.1 (A), R13.1, U5.20 (VINT)
VMOT: C8.1, C10.1, C11.1, C12.1, R24.1, U5.18 (VM), U5.19 (VM); also elsewhere on the board

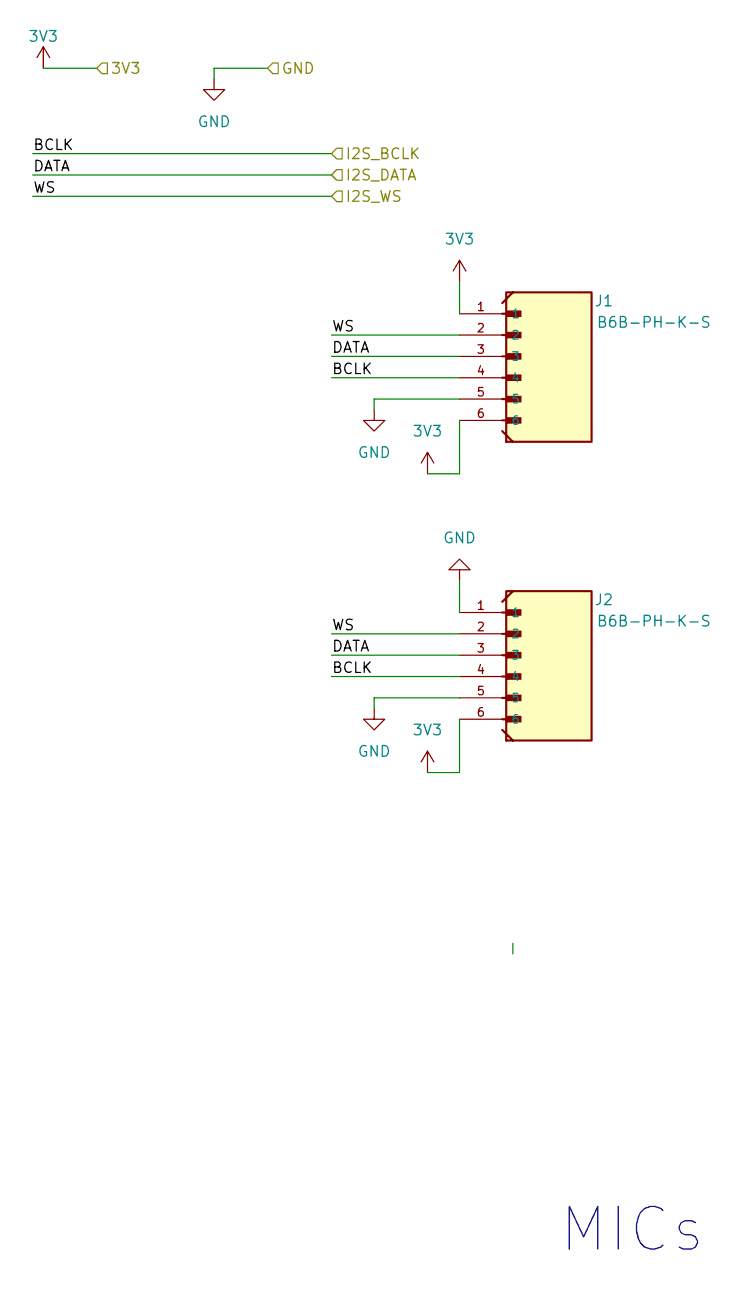
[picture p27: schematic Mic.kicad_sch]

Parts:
J1, J2: B6B-PH-K-S; JST_B6B-PH-K-S

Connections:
3V3: J1.1, J1.6, J2.6; also elsewhere on the board
GND: J1.5, J2.1, J2.5; also elsewhere on the board
I2S_BCLK: J1.4, J2.4; also elsewhere on the board
I2S_DATA: J1.3, J2.3; also elsewhere on the board
I2S_WS: J1.2, J2.2; also elsewhere on the board

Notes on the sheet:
MICs

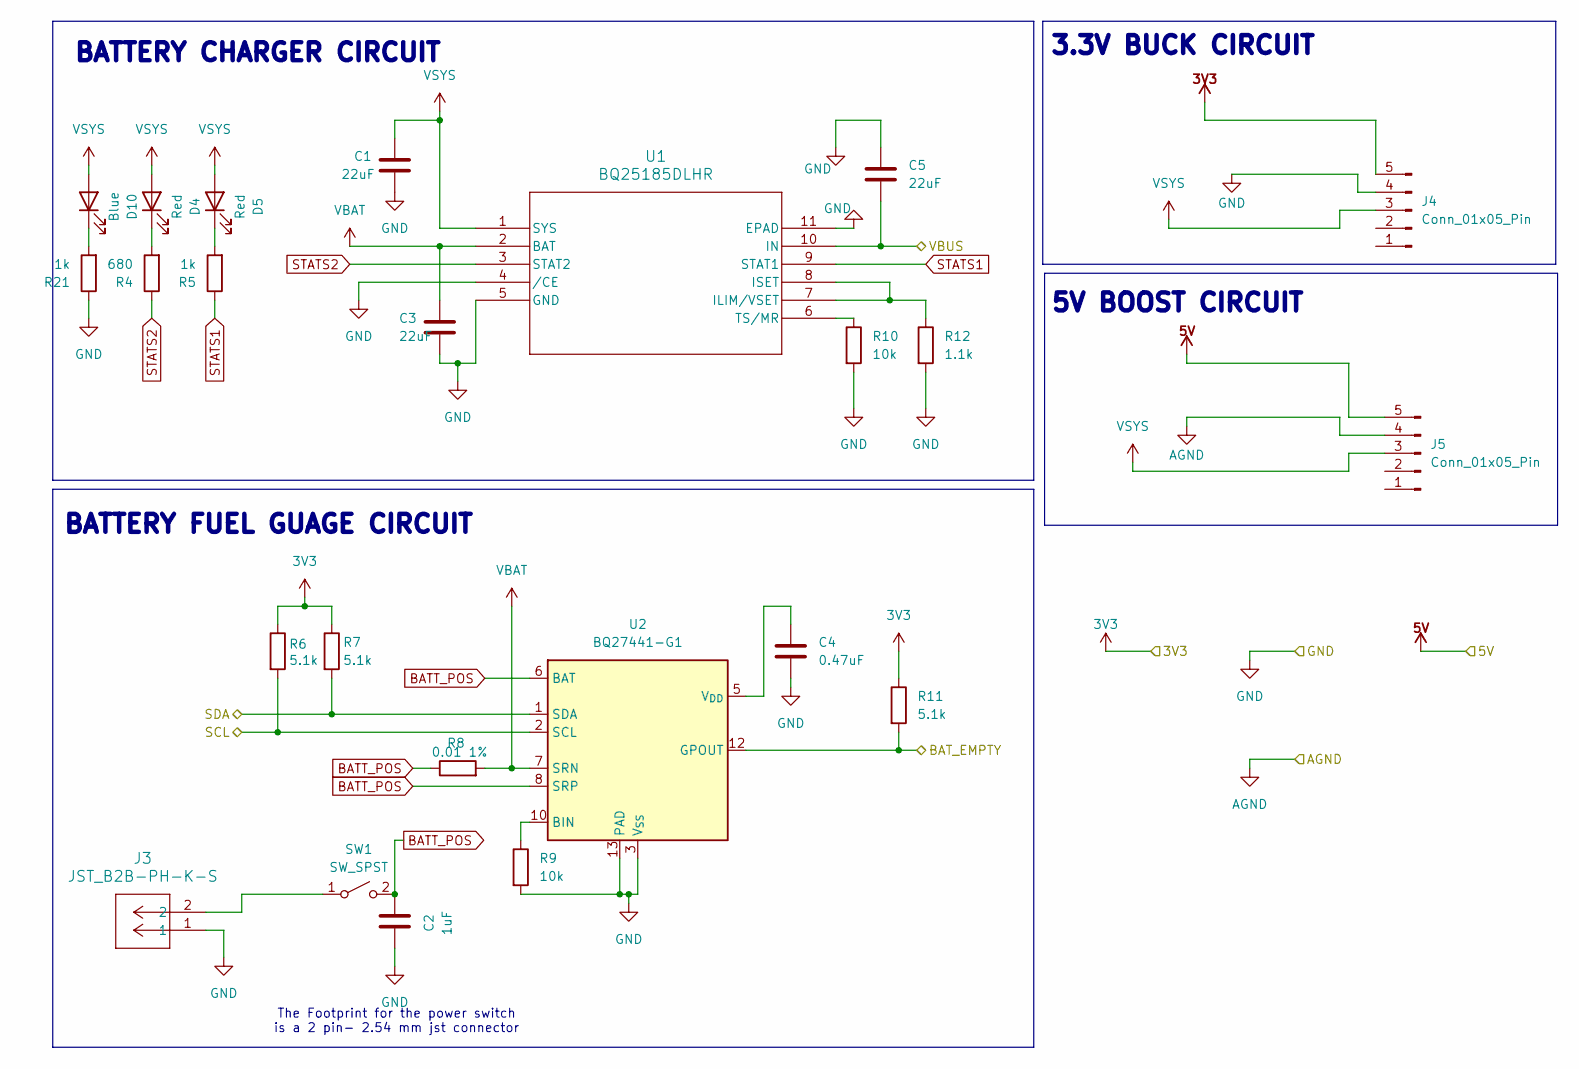
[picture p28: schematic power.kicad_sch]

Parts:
C1, C3, C5: 22uF; C_0805_2012Metric
C2: 1uF; C_0805_2012Metric
C4: 0.47uF; C_0805_2012Metric
D4, D5: Red; LED_0805_2012Metric_Pad1.15x1.40mm_HandSolder
D10: Blue; LED_0805_2012Metric_Pad1.15x1.40mm_HandSolder
J3: JST_B2B-PH-K-S
J4, J5: Conn_01x05_Pin; PinHeader_1x05_P2.54mm_Vertical
R4: 680; R_0805_2012Metric
R5, R21: 1k; R_0805_2012Metric
R6, R7, R11: 5.1k; R_0805_2012Metric
R8: 0.01 1%; R_0805_2012Metric
R9, R10: 10k; R_0805_2012Metric
R12: 1.1k; R_0805_2012Metric
SW1: SW_SPST; JST_B2B-PH-K-S
U1: BQ25185DLHR; WSON10_DLH_TEX
U2: BQ27441-G1; Texas_S-PDSO-N12

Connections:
3V3: J4.5, R6.1, R7.1, R11.1; also elsewhere on the board
5V: J5.5; also elsewhere on the board
AGND: J5.4; also elsewhere on the board
BATT_POS: C2.2, R8.1, SW1.2 (B), U2.6 (BAT), U2.8 (SRP)
BAT_EMPTY: R11.2, U2.12 (GPOUT); also elsewhere on the board
GND: C1.2, C2.1, C3.2, C4.2, C5.1, J3.1, J4.4, R9.2, R10.2, R12.2, R21.1, U1.4 (/CE), U1.5 (GND), U1.11 (EPAD), U2.3 (V_{SS}), U2.13 (PAD); also elsewhere on the board
unnamed: D4.1 (K), R4.2
unnamed: D5.1 (K), R5.2
unnamed: D10.1 (K), R21.2
unnamed: J3.2, SW1.1 (A)
unnamed: R12.1, U1.7 (ILIM/VSET), U1.8 (ISET)
unnamed: R10.1, U1.6 (TS/MR)
unnamed: R9.1, U2.10 (BIN)
unnamed: C4.1, U2.5 (V_{DD})
SCL: R6.2, U2.2 (SCL); also elsewhere on the board
SDA: R7.2, U2.1 (SDA); also elsewhere on the board
STATS1: R5.1, U1.9 (STAT1)
STATS2: R4.1, U1.3 (STAT2)
VBAT: C3.1, R8.2, U1.2 (BAT), U2.7 (SRN)
VBUS: C5.2, U1.10 (IN); also elsewhere on the board
VSYS: C1.1, D4.2 (A), D5.2 (A), D10.2 (A), J4.3, J5.3, U1.1 (SYS)

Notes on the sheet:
3.3V BUCK CIRCUIT
BATTERY CHARGER CIRCUIT
BATTERY FUEL GUAGE CIRCUIT
The Footprint for the power switch is a 2 pin- 2.54 mm jst connector
5V BOOST CIRCUIT

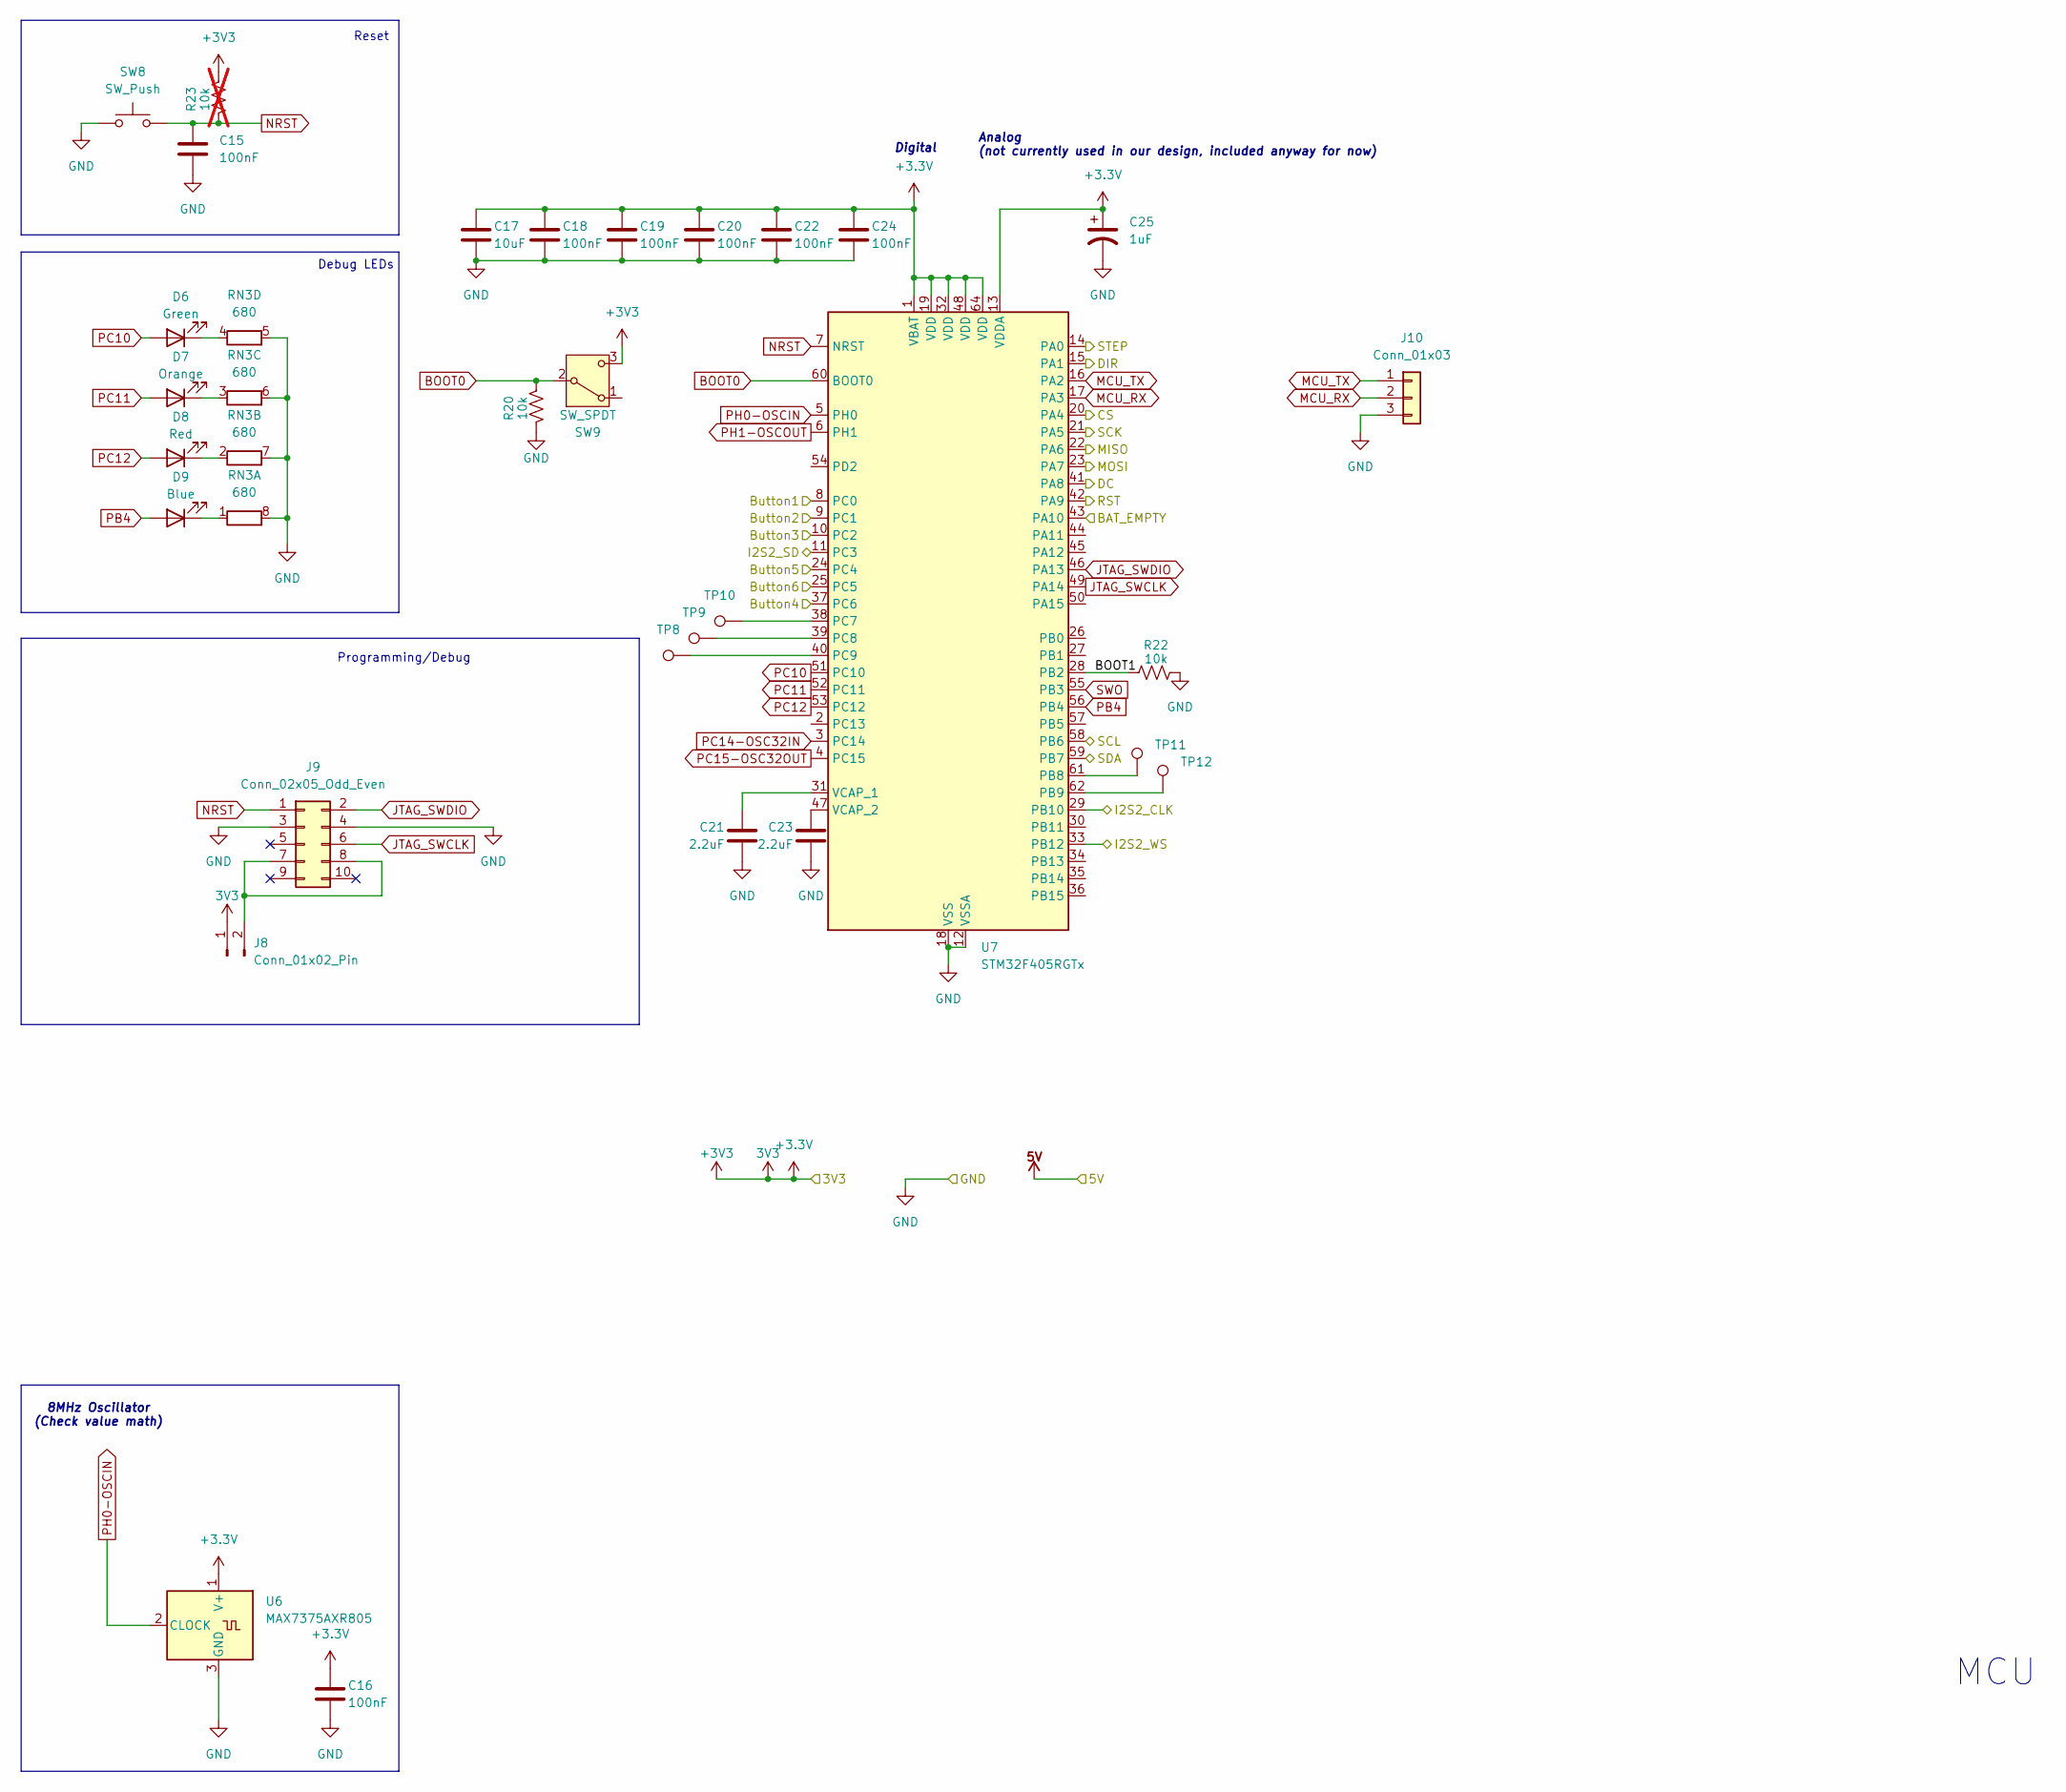
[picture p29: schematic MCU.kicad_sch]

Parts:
C15, C16, C18, C19, C20, C22, C24: 100nF; C_0805_2012Metric
C17: 10uF; C_0805_2012Metric
C21, C23: 2.2uF; C_0805_2012Metric
C25: 1uF; C_1206_3216Metric_Pad1.33x1.80mm_HandSolder
D6: Green; LED_0805_2012Metric_Pad1.15x1.40mm_HandSolder
D7: Orange; LED_0805_2012Metric_Pad1.15x1.40mm_HandSolder
D8: Red; LED_0805_2012Metric_Pad1.15x1.40mm_HandSolder
D9: Blue; LED_0805_2012Metric_Pad1.15x1.40mm_HandSolder
J8: Conn_01x02_Pin; PinHeader_1x02_P2.54mm_Vertical
J9: Conn_02x05_Odd_Even; IDC-Header_2x05_P2.54mm_Vertical
J10: Conn_01x03; PinHeader_1x03_P2.54mm_Vertical
R20, R22: 10k; R_0805_2012Metric
R23: 10k; R_0805_2012Metric; not fitted
RN3: 680; RESCAXS80P320X160X60-8N
SW8: SW_Push; SW_TS04-66-65-BK-160-SMT
SW9: SW_SPDT; SW_SPDT_PCM12
TP8, TP9, TP10, TP11, TP12: TestPoint_THTPad_D0.8mm_Drill0.4mm
U6: MAX7375AXR805; SOT-323_SC-70
U7: STM32F405RGTx; LQFP-64_10x10mm_P0.5mm

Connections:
3V3: C16.1, C17.1, C18.1, C19.1, C20.1, C22.1, C24.1, C25.1, J8.1, R23.1, SW9.3 (C), U6.1 (V+), U7.1 (VBAT), U7.13 (VDDA), U7.19 (VDD), U7.32 (VDD), U7.48 (VDD), U7.64 (VDD); also elsewhere on the board
/MCU/BOOT1: R22.1, U7.28 (PB2)
BAT_EMPTY: U7.43 (PA10); also elsewhere on the board
BOOT0: R20.1, SW9.2 (B), U7.60 (BOOT0)
Button1: U7.8 (PC0); also elsewhere on the board
Button2: U7.9 (PC1); also elsewhere on the board
Button3: U7.10 (PC2); also elsewhere on the board
Button4: U7.37 (PC6); also elsewhere on the board
Button5: U7.24 (PC4); also elsewhere on the board
Button6: U7.25 (PC5); also elsewhere on the board
CS: U7.20 (PA4); also elsewhere on the board
DC: U7.41 (PA8); also elsewhere on the board
DIR: U7.15 (PA1); also elsewhere on the board
GND: C15.2, C16.2, C17.2, C18.2, C19.2, C20.2, C21.2, C22.2, C23.2, C24.2, C25.2, J9.3, J9.4, J10.3, R20.2, R22.2, RN3.5 (R4.2), RN3.6 (R3.2), RN3.7 (R2.2), RN3.8 (R1.2), SW8.1, U6.3 (GND), U7.12 (VSSA), U7.18 (VSS), U7.63 (VSS); also elsewhere on the board
I2S_BCLK: U7.29 (PB10); also elsewhere on the board
I2S_DATA: U7.11 (PC3); also elsewhere on the board
I2S_WS: U7.33 (PB12); also elsewhere on the board
JTAG_SWCLK: J9.6, U7.49 (PA14)
JTAG_SWDIO: J9.2, U7.46 (PA13)
MCU_RX: J10.2, U7.17 (PA3)
MCU_TX: J10.1, U7.16 (PA2)
NRST: C15.1, J9.1, R23.2, SW8.2, U7.7 (NRST)
unnamed: D6.1 (K), RN3.4 (R4.1)
unnamed: D7.1 (K), RN3.3 (R3.1)
unnamed: D8.1 (K), RN3.2 (R2.1)
unnamed: D9.1 (K), RN3.1 (R1.1)
unnamed: J8.2, J9.7, J9.8
unnamed: TP11.1, U7.61 (PB8)
unnamed: TP12.1, U7.62 (PB9)
unnamed: TP10.1, U7.38 (PC7)
unnamed: TP9.1, U7.39 (PC8)
unnamed: TP8.1, U7.40 (PC9)
unnamed: C21.1, U7.31 (VCAP_1)
unnamed: C23.1, U7.47 (VCAP_2)
PB4: D9.2 (A), U7.56 (PB4)
PC10: D6.2 (A), U7.51 (PC10)
PC11: D7.2 (A), U7.52 (PC11)
PC12: D8.2 (A), U7.53 (PC12)
PC14-OSC32IN: U7.3 (PC14)
PC15-OSC32OUT: U7.4 (PC15)
PH0-OSCIN: U6.2 (CLOCK), U7.5 (PH0)
PH1-OSCOUT: U7.6 (PH1)
RST: U7.42 (PA9); also elsewhere on the board
SCL: U7.58 (PB6); also elsewhere on the board
SDA: U7.59 (PB7); also elsewhere on the board
SPI1_MISO: U7.22 (PA6); also elsewhere on the board
SPI1_MOSI: U7.23 (PA7); also elsewhere on the board
SPI1_SCK: U7.21 (PA5); also elsewhere on the board
STEP: U7.14 (PA0); also elsewhere on the board
SWO: U7.55 (PB3)

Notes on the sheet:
Digital
MCU
8MHz Oscillator (Check value math)
Analog (not currently used in our design, included anyway for now)
Programming/Debug
Debug LEDs
Reset

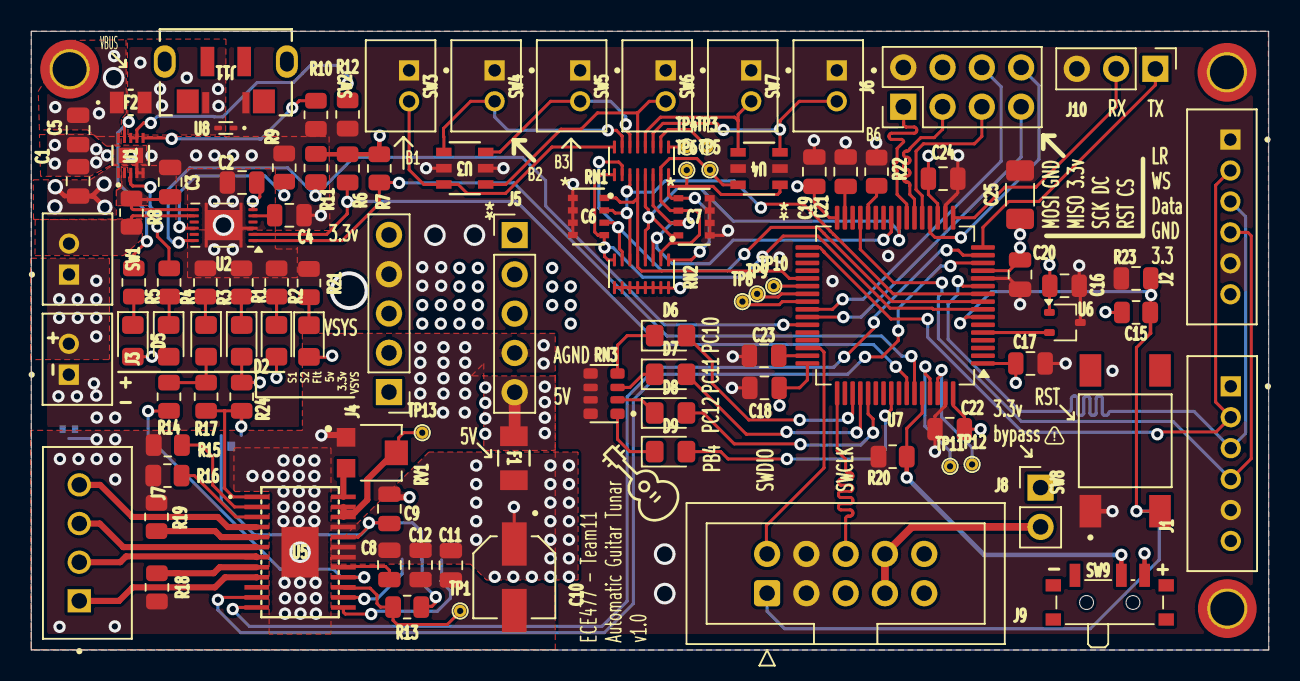
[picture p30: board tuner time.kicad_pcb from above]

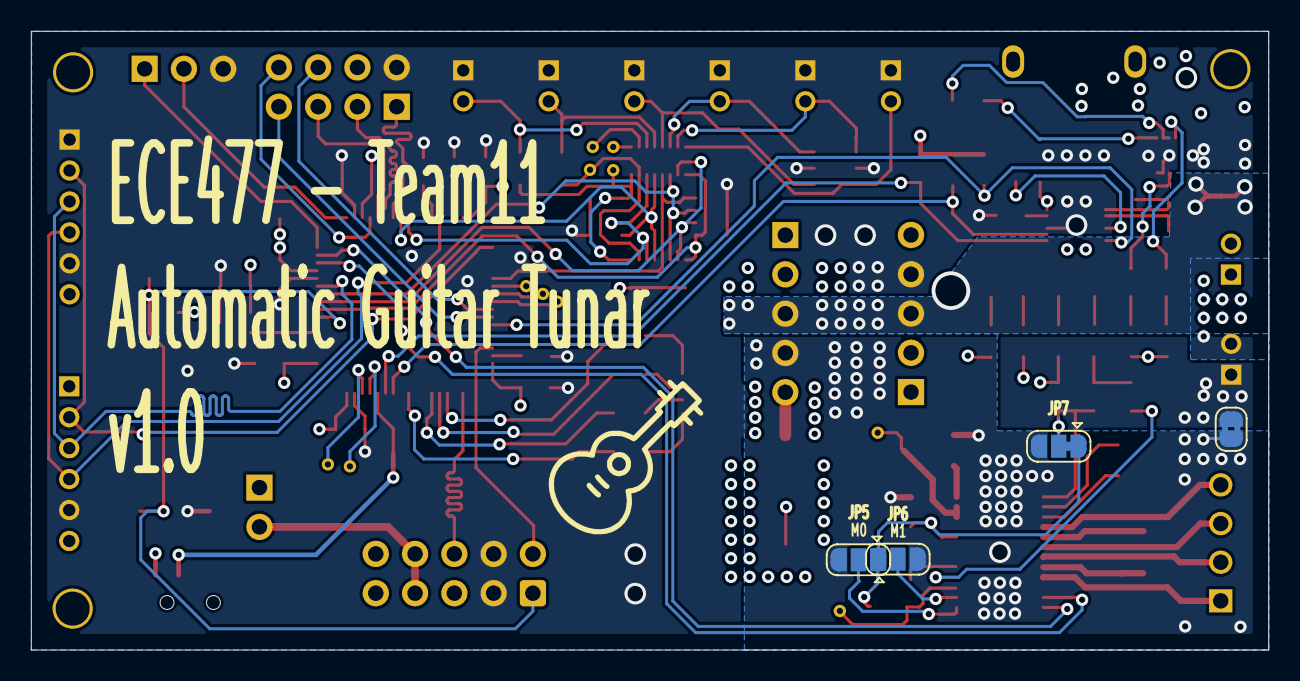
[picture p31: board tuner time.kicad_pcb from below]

Board: 4 copper layers, 80.0 x 40.0 mm, 109 parts (4 on the bottom side), 95 nets.

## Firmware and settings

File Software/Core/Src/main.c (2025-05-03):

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
/* Includes ------------------------------------------------------------------*/
#include "main.h"
// #include "stm32f407xx.h"
#include "extitimer.h"

/* USER CODE BEGIN Includes */
#include "stdio.h"
#include "arm_math.h"
#include <errno.h>
#include <sys/unistd.h>
#include <string.h>
/* USER CODE END Includes */

/* USER CODE BEGIN PTD */
typedef struct {
  float32_t magnitude;
  uint16_t bin_index;
} FrequencyPeak;
/* USER CODE END PTD */

/* USER CODE BEGIN PD */
#define TAG_TOP_TEN_FREQ
//#define TAG_FFT_ALL
#define BATTERY_CONNECTED
#define MIC_CONNECTED
/* USER CODE END PD */

/* USER CODE BEGIN PM */
#define SAMPLES_TO_GET 5.0f
void nano_wait(int t); // FROM ECE362 LABS - might need to tweak
uint16_t charge_buffer; 
state_t state; 
char data_c[2];
char output_batt[20];
uint8_t sample_count = 0;
float32_t prev_sample = 0.0f; 
float32_t sum_samps = 0.0f;
float32_t avrg_freq;
uint8_t ready_to_process = 0; 
const float32_t standard_tuning[6] =
{
    82.41,  // E
    110,    // A
    146.83, // D
    196,    // G
    246.94, // B
    329.63  // E
};

const float32_t tuning_ranges[6] =
{
    20,
    20,
    25,
    25,
    40,
    40
};

float32_t freq_diff;

float32_t interpolated_freq;
float32_t interpolated_mag;

u8 tuning_i = 0;
float32_t frequency;
/* USER CODE END PM */

I2S_HandleTypeDef hi2s2;
DMA_HandleTypeDef hdma_spi2_rx;

UART_HandleTypeDef huart2;
DMA_HandleTypeDef hdma_usart2_tx;

/* USER CODE BEGIN PV */ 
// Generated by FIRfilterCoeff.py
static const float32_t h[] = {
  0.000000000000000000,
  0.000000007212970196,
  0.000000055131376202,
  0.000000171543973319,
  0.000000360266179641,
  0.000000594874965645,
  0.000000818935100534,
  0.000000953269382216,
  0.000000909594621891,
  0.000000608652866177,
  0.000000000000000000,
  -0.000000919966594950,
  -0.000002095239515927,
  -0.000003405721984287,
  -0.000004673080368682,
  -0.000005677570045858,
  -0.000006184832442803,
  -0.000005979993496011,
  -0.000004904940557073,
  -0.000002893643362343,
  0.000000000000000000,
  0.000003586954564869,
  0.000007544518199528,
  0.000011436700949649,
  0.000014753424308920,
  0.000016965877505996,
  0.000017592859001211,
  0.000016270823733091,
  0.000012818966330517,
  0.000007290250698265,
  0.000000000000000000,
  -0.000008474487081748,
  -0.000017326945232164,
  -0.000025587771714763,
  -0.000032218218776113,
  -0.000036225105432006,
  -0.000036784580473335,
  -0.000033361080813736,
  -0.000025806670682806,
  -0.000014426673819225,
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
};


#define I2S_BUFFER_SIZE 1024 * 4 * 2
int16_t  data_i2s[I2S_BUFFER_SIZE];
float32_t mic1_data1[I2S_BUFFER_SIZE / 4], mic1_data2[I2S_BUFFER_SIZE / 4];
volatile int16_t sample_i2s;
volatile uint8_t button_flag, start_stop_recording;
volatile uint8_t  half_i2s, full_i2s;
arm_rfft_fast_instance_f32 fft_audio_instance;

#define FILTER_TAP_NUM 461

arm_fir_instance_f32 fir_instance;
float32_t fir_state[I2S_BUFFER_SIZE / 4 + FILTER_TAP_NUM - 1];



#define UART_TX_BUFFER_SIZE 512 
static uint32_t uart_tx_buffer[512];
static volatile uint8_t uart_tx_busy = 0;

/* USER CODE END PV */

void SystemClock_Config(void);
static void MX_GPIO_Init(void);
static void MX_DMA_Init(void);
static void MX_I2S2_Init(void);
static void MX_USART2_UART_Init(void);
/* USER CODE BEGIN 0 */
void HAL_UART_TxCpltCallback(UART_HandleTypeDef *huart)
{
    if (huart->Instance == USART2) {
        uart_tx_busy = 0;
    }
}
int compare_peaks(const void* a, const void* b) {
  FrequencyPeak* peak_a = (FrequencyPeak*)a;
  FrequencyPeak* peak_b = (FrequencyPeak*)b;
  if (peak_a->magnitude > peak_b->magnitude) return -1;
  if (peak_a->magnitude < peak_b->magnitude) return 1;
  return 0;
}

void send_top_frequencies(float32_t* fft_data, uint16_t fft_size, uint32_t sample_rate) {
  uint16_t useful_bins = fft_size / 2;
  FrequencyPeak max_peak = {0};
  float32_t max_magnitude = 0;
  uint16_t max_bin = 0;
  
  float32_t freq_resolution = (float32_t)sample_rate / fft_size;
  for (uint16_t i = 1; i < useful_bins - 1; i++) {
      float32_t frequency = i * freq_resolution;
      if ((frequency > 30.0f) && (frequency < 700.0f)) {
          if (fft_data[i] > fft_data[i-1] && fft_data[i] > fft_data[i+1]) {
              if (fft_data[i] > max_magnitude) {
                  max_magnitude = fft_data[i];
                  max_bin = i;
              }
          }
      }
  }
  
  // quadratic interpolation - used to better esetimate the frequency from the bins (thank you internet)
  if (max_bin > 0) {
      float32_t alpha = fft_data[max_bin - 1];
      float32_t beta = fft_data[max_bin];
      float32_t gamma = fft_data[max_bin + 1];
      float32_t p = 0.5f * (alpha - gamma) / (alpha - 2*beta + gamma);
      interpolated_freq = (max_bin + p) * freq_resolution;
      interpolated_mag = beta - 0.25f * (alpha - gamma) * p;

      char buffer[100];
      int freq_int = (int)interpolated_freq;
      int freq_dec = (int)((interpolated_freq - freq_int) * 100); 
      int mag_int = (int)interpolated_mag;
      int mag_dec = (int)((interpolated_mag - mag_int) * 100);
      
      strcpy(buffer, "");
      strcat(buffer, "Freq: ");
      char freq_str[20];
      sprintf(freq_str, "%3d.%02d Hz, ", freq_int, freq_dec);
      strcat(buffer, freq_str);
      strcat(buffer, "Mag: ");
      char mag_str[20];
      sprintf(mag_str, "%3d.%02d\r\n", mag_int, mag_dec);
      strcat(buffer, mag_str);
      send_uart(buffer, strlen(buffer));

  }
  
  char *footer = "\r\n";
  send_uart(footer, strlen(footer));
}

void TIM3_IRQHandler(void)
{
  TIM3 -> SR &= ~TIM_SR_UIF;
  if((GPIOC->IDR & (1 << 1)) == 0) // held, active low buttons
  {
    if(state == FREE_SPIN)
    {
      OLED_DrawString(0, 30, WHITE, BLACK, "*", 12);
      drive_motor(30, direct);
    }
    else // STANDARD TUNING STATE
    {
      OLED_DrawString(90, 30, WHITE, BLACK, "*", 12);
      // char buffer[100];
      // int freq_int = (int)interpolated_freq;
      // int freq_dec = (int)((interpolated_freq - freq_int) * 100); 
      // int mag_int = (int)interpolated_mag;
      // int mag_dec = (int)((interpolated_mag - mag_int) * 100);
      
      // strcpy(buffer, "");
      // strcat(buffer, "Freq_tim: ");
      // char freq_str[20];
      // sprintf(freq_str, "%3d.%02d Hz, ", freq_int, freq_dec);
      // strcat(buffer, freq_str);
      // strcat(buffer, "Mag_tim: ");
      // char mag_str[20];
      // sprintf(mag_str, "%3d.%02d\r\n", mag_int, mag_dec);
      // strcat(buffer, mag_str);
      // send_uart(buffer, strlen(buffer));
      #ifdef MIC_CONNECTED
      // int int_fact = (int)(interpolated_freq / standard_tuning[state]);
      // float32_t harmonic_factor = (float32_t) int_fact; 
      // // i2s_dma_enable(); // allow mic to read 
      // // if curr_freq is OVER, - value, if UNDER, + value
      // freq_diff = (harmonic_factor*standard_tuning[state]) - interpolated_freq;
      // Logic for standard tuning states here!
      float32_t current_goal = standard_tuning[state];
      float32_t harmonic_factor = (interpolated_freq / (standard_tuning[state]));
      int rounded_factor = (int)(harmonic_factor + 0.5f);
      // float32_t current_goal = standard_tuning[state];

      if((interpolated_freq >= ((rounded_factor*standard_tuning[state]) - tuning_ranges[state])) && (interpolated_freq <= ((rounded_factor*standard_tuning[state]) + tuning_ranges[state]))) // if it's close to current goal, assume pluck
      {
        if((prev_sample >= interpolated_freq - 5) && (prev_sample <= interpolated_freq + 5)) // if sample is close enough to last, pluck should produce at least 3
        {
          sum_samps += prev_sample;
          sample_count++;
        }
        else // NO MATCH
        {
          sample_count = 0;
          sum_samps = 0; 
        }
        if(sample_count > (int)SAMPLES_TO_GET) // if we've gather 3 samples by the conditions above...
        {
          // avrg_freq = sum_samps / SAMPLES_TO_GET; // average the pluck
          avrg_freq = (prev_sample + interpolated_freq) / 2;
          sum_samps = 0;
          ready_to_process = 1;
        }
      }

      if(ready_to_process) // if we got three samples close enough to goal/its harmonics...
      {
        // if(avrg_freq <= 500.0f && avrg_freq >= 30.0f) // add base range
        // {
        // if curr_freq is OVER, - value, if UNDER, + value
        freq_diff = avrg_freq - (rounded_factor*standard_tuning[state]);
        if(abs(freq_diff) <= 2)
        {
          OLED_DrawString(84, 60, B_Color, BLACK, "SUCCESS", 12);
          OLED_DrawString(90, 72, B_Color, BLACK, "<  >", 12);
          TIM3 -> CR1 &= ~TIM_CR1_CEN; // MIGHT NEED TO REMOVE THIS
        }
        else
        {
          if(abs(freq_diff) >= 10) // big spin 
          {
              if(freq_diff > 0) // positive
              {
                  drive_motor(20, 0);
              }
              else // negative
              {
                  drive_motor(20, 1);
              }
          }
          else if(abs(freq_diff) >= 7)
          {
              if(freq_diff > 0) // positive
              {
                  drive_motor(10, 0);
              }
              else // negative
              {
                  drive_motor(10, 1);
              }
          }
          else if(abs(freq_diff) >= 2)
          {
              if(freq_diff > 0) // positive
              {
                  drive_motor(5, 0);
              }
              else // negative
              {
                  drive_motor(5, 1);
              }
          }
          // else
          // {
          //     if(freq_diff > 0) // positive
          //     {
          //         drive_motor(2, 0);
          //     }
          //     else // negative
          //     {
          //         drive_motor(2, 1);
          //     }
          // }
        }
        // }
        ready_to_process = 0; // clear to gather new pluck
      }
      #endif
      }
    prev_sample = interpolated_freq; // for gathering 3 samples aka a "pluck"
  }
  else 
  {
      TIM3 -> CR1 &= ~TIM_CR1_CEN; // disable timer
      if (state == FREE_SPIN) OLED_DrawString(0, 30, WHITE, BLACK, "  ", 12);
      else OLED_DrawString(90, 30, WHITE, BLACK, "  ", 12);
      // i2s_dma_disable(); // stop mic from reading to memory
      sample_count = 0; 
      ready_to_process = 0; 
  }
}

void TIM2_IRQHandler(void)
{
    TIM2 -> SR &= ~TIM_SR_UIF;
    char buf_freq[20];
    sprintf(buf_freq, "%d", (int)interpolated_freq);
    OLED_DrawString(80, 20, WHITE, BLACK, "   ", 16);
    OLED_DrawString(80, 20, WHITE, BLACK, buf_freq, 16);
}

// int _write(int file, char *ptr, int len)
// {
//     if (file != STDOUT_FILENO && file != STDERR_FILENO) {
//         errno = EBADF;
//         return -1;
//     }

//     HAL_UART_Transmit(&huart2, (uint8_t*)ptr, len, 100);
//     return len;
// }

void send_uart(char *ptr, int len)
{
  HAL_UART_Transmit(&huart2, (uint8_t*)ptr, len, 100);
}


// void send_fft_data(float32_t* fft_data, size_t data_size)
// {
//     while (uart_tx_busy) {
//         // Wait for previous transfer to complete
//     }

//     // Copy data directly as it's already 32-bit aligned
//     memcpy(uart_tx_buffer, fft_data, data_size * 4);
    
//     // Ensure the end marker is properly set
//     uart_tx_buffer[data_size-1] = ('>'<<24|'>'<<16|'>'<<8|'>');

//     uart_tx_busy = 1;
//     HAL_UART_Transmit_DMA(&huart2, (uint8_t*)uart_tx_buffer, data_size * 4);
// }



/* USER CODE END 0 */

/**
  * @brief  The application entry point.
  * @retval int
  */
int main(void)
{

  /* USER CODE BEGIN 1 */
  uint8_t uart_counter = 0;
  /* USER CODE END 1 */

  /* MCU Configuration--------------------------------------------------------*/

  /* Reset of all peripherals, Initializes the Flash interface and the Systick. */
  HAL_Init();

  /* USER CODE BEGIN Init */
  init_spi1_oled(); 
  init_exti();
  init_i2c_BQ27441(); 
  init_DRV();

  OLED_Setup(); 
  OLED_Clear(BLACK); 

  init_tim2();
  init_tim3();
  init_tim4(); 
  // Check battery charge and prevent boot if too low:
  #ifdef BATTERY_CONNECTED
  i2c_send_address(BQ27441_COMMAND_SOC); // get percent charge
  i2c_read_address(2, data_c);
  charge_buffer = (data_c[1] << 8) | data_c[0];
  #else
  charge_buffer = 10; // hardcode for testing
  #endif
  if(charge_buffer <= 3) // if percent charge is less than 3
  {
      OLED_DrawString(32, 50, C_Color, BLACK, "LOW BATT", 16);
      OLED_DrawString(34, 66, WHITE, BLACK, "Power off", 12);
      OLED_DrawString(34, 78, WHITE, BLACK, "and charge", 12);
      // while(1); // hold here until power off
  }
  else
  {
      state = MAIN_MENU; 
      OLED_WriteMenu();
  }
  /* USER CODE END Init */

  /* Configure the system clock */
  SystemClock_Config();

  /* Initialize all configured peripherals */
  MX_GPIO_Init();
  MX_DMA_Init();
  MX_I2S2_Init();
  MX_USART2_UART_Init();
  /* USER CODE BEGIN 2 */
  HAL_I2S_DMAStop(&hi2s2);
  HAL_Delay(500);
  arm_rfft_fast_init_f32(&fft_audio_instance, I2S_BUFFER_SIZE / 4);
  arm_fir_init_f32(&fir_instance, FILTER_TAP_NUM, (float32_t *)h, fir_state, I2S_BUFFER_SIZE / 4);

  char *msg = "Hello World!\r\n";
  send_uart(msg, strlen(msg));

  start_stop_recording = 1;

  msg = "start_recording\r\n";
  send_uart(msg, strlen(msg));
  HAL_GPIO_WritePin(GPIOC, GPIO_PIN_12, GPIO_PIN_SET); // Turn on the LED
  HAL_GPIO_WritePin(GPIOB, GPIO_PIN_4, GPIO_PIN_SET); // Turn on the LED
  HAL_Delay(1000);
  HAL_GPIO_WritePin(GPIOC, GPIO_PIN_12, GPIO_PIN_RESET); // Turn off the LED
  HAL_GPIO_WritePin(GPIOB, GPIO_PIN_4, GPIO_PIN_RESET); // Turn off the LED
  HAL_I2S_Receive_DMA(&hi2s2, (uint16_t *)data_i2s, sizeof(data_i2s)/2);
  HAL_Delay(1000);
  full_i2s = 0;
  half_i2s = 0;
  /* USER CODE END 2 */

  /* Infinite loop */
  /* USER CODE BEGIN WHILE */
  while (1)
  {
	  HAL_GPIO_TogglePin(GPIOB, GPIO_PIN_4);  // Toggle PB4
	  // HAL_Delay(10);  
        // Delay for 500ms (0.5 seconds)
    // Add LED flashing during recording
    static uint32_t led_timestamp = 0;
    if(start_stop_recording)
    {
        if(HAL_GetTick() - led_timestamp > 500) // Flash every 500ms
        {
            HAL_GPIO_TogglePin(GPIOC, GPIO_PIN_12); // Toggle the LED pin
            led_timestamp = HAL_GetTick();
        }
    }


    /* USER CODE END WHILE */
  }
}
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
/* USER CODE BEGIN 4 */
int _write(int file, char *ptr, int len)
{
	int DataIdx;

	for (DataIdx = 0; DataIdx < len; DataIdx++)
	{
		ITM_SendChar(*ptr++);
	}
	return len;
}
//	l,r,l,r,l,

// RxHalfCpltCallback modification
void HAL_I2S_RxHalfCpltCallback(I2S_HandleTypeDef *hi2s)
{
  static float32_t data_out_fft1[I2S_BUFFER_SIZE / 4];
  static float32_t filtered_data[I2S_BUFFER_SIZE / 4];

    HAL_GPIO_TogglePin(GPIOC, GPIO_PIN_11);
    half_i2s = 1;
    
    // Process the data
    for(int i = 0; i < I2S_BUFFER_SIZE / 4; i++ )
    {
        mic1_data1[i] = (float32_t)data_i2s[i * 2];
    }
    
    // Apply FIR filter
    arm_fir_f32(&fir_instance, mic1_data1, filtered_data, I2S_BUFFER_SIZE / 4);
    
    // Apply FFT to filtered data
    arm_rfft_fast_f32(&fft_audio_instance, filtered_data, data_out_fft1, 0);
    arm_cmplx_mag_f32(data_out_fft1, data_out_fft1, I2S_BUFFER_SIZE / 8);
    data_out_fft1[0] = 0;  // bias removal

    // Send data based on defined tags
#ifdef TAG_TOP_TEN_FREQ
    send_top_frequencies(data_out_fft1, I2S_BUFFER_SIZE / 4, 16000);
#endif

#ifdef TAG_FFT_ALL
    uint8_t start_marker = 0xAA;
    HAL_UART_Transmit(&huart2, &start_marker, 1, 10);
    HAL_UART_Transmit(&huart2, (uint8_t *)data_out_fft1, I2S_BUFFER_SIZE / 8 * sizeof(float32_t), 100);
    uint8_t end_marker = 0x55;
    HAL_UART_Transmit(&huart2, &end_marker, 1, 10);
#endif
}

// RxCpltCallback modification
void HAL_I2S_RxCpltCallback(I2S_HandleTypeDef *hi2s)
{
  static float32_t data_out_fft2[I2S_BUFFER_SIZE / 4];
  static float32_t filtered_data[I2S_BUFFER_SIZE / 4];
    HAL_GPIO_TogglePin(GPIOC, GPIO_PIN_12);
    full_i2s = 1;
    
    for(int i = 0; i < I2S_BUFFER_SIZE / 4; i++ )
    {
        mic1_data2[i] = (float32_t)data_i2s[i * 2 + I2S_BUFFER_SIZE / 2];
    }
    
    arm_fir_f32(&fir_instance, mic1_data2, filtered_data, I2S_BUFFER_SIZE / 4);
    
    arm_rfft_fast_f32(&fft_audio_instance, filtered_data, data_out_fft2, 0);
    arm_cmplx_mag_f32(data_out_fft2, data_out_fft2, I2S_BUFFER_SIZE / 8);
    data_out_fft2[0] = 0;  // bias removal

    // Send data based on defined tags
#ifdef TAG_TOP_TEN_FREQ
    send_top_frequencies(data_out_fft2, I2S_BUFFER_SIZE / 4, 16000);
#endif

#ifdef TAG_FFT_ALL
    uint8_t start_marker = 0xAA;
    HAL_UART_Transmit(&huart2, &start_marker, 1, 10);
    HAL_UART_Transmit(&huart2, (uint8_t *)data_out_fft2, I2S_BUFFER_SIZE / 8 * sizeof(float32_t), 100);
    uint8_t end_marker = 0x55;
    HAL_UART_Transmit(&huart2, &end_marker, 1, 10);
#endif

    // Restart DMA
    HAL_I2S_Receive_DMA(&hi2s2, (uint16_t *)data_i2s, sizeof(data_i2s)/2);
}


/* USER CODE END 4 */
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


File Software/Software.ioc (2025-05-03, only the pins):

Mcu.UserName=STM32F405RGTx
PA2.Signal=USART2_TX
PA3.Signal=USART2_RX
PB10.Signal=I2S2_CK
PB12.Signal=I2S2_WS
PB4.Signal=GPIO_Output
PC10.Signal=GPIO_Output
PC11.Signal=GPIO_Output
PC12.Signal=GPIO_Output
PC3.Signal=I2S2_SD

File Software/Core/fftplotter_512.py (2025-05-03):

import matplotlib.pyplot as plt
import numpy as np
from matplotlib.animation import FuncAnimation
import serial
import struct
from threading import Thread
from collections import deque

class FFTPlotter:
    def __init__(self, port='COM3', baud=115200):
        # UART configuration
        try:
            self.uart = serial.Serial(port, baud,
                                    parity=serial.PARITY_NONE,
                                    stopbits=serial.STOPBITS_ONE,
                                    bytesize=serial.EIGHTBITS,
                                    timeout=1)
        except serial.SerialException as e:
            print(f"Failed to open serial port {port}: {e}")
            raise
        
        # FFT parameters
        self.N = 1024  # WAV_WRITE_SAMPLE_COUNT/4 from firmware
        self.sample_rate = 16000  # Match with I2S config (48kHz)
        self.freq_range = np.linspace(0, self.sample_rate/2, self.N//2)  # Frequency axis
        
        # Plot setup
        plt.style.use('dark_background')  # Optional: use dark theme
        self.fig, self.ax = plt.subplots(figsize=(12, 6))
        self.fft_values = np.zeros(self.N//2)
        self.max_freq_points = deque(maxlen=10)  # Store last 10 peak frequencies
        
        # Data reading
        self.buffer = bytearray()
        self.START_MARKER = 0xAA
        self.END_MARKER = 0x55
        self.expected_data_size = (self.N//2) * 4  # Size in bytes of float32 array
        
        # Start reading thread
        self.running = True
        self.thread = Thread(target=self._read_uart, daemon=True)
        self.thread.start()

    def _read_uart(self):
        SEARCHING_START = 0
        READING_DATA = 1
        state = SEARCHING_START
        
        while self.running:
            try:
                if self.uart.in_waiting > 0:
                    if state == SEARCHING_START:
                        # Look for start marker
                        byte = self.uart.read(1)[0]
                        if byte == self.START_MARKER:
                            self.buffer = bytearray()
                            state = READING_DATA
                    
                    elif state == READING_DATA:
                        # Read expected amount of data
                        remaining = self.expected_data_size - len(self.buffer)
                        if remaining > 0:
                            data = self.uart.read(min(remaining, self.uart.in_waiting))
                            self.buffer.extend(data)
                            
                            if len(self.buffer) == self.expected_data_size:
                                # Check end marker
                                end_byte = self.uart.read(1)
                                if end_byte and end_byte[0] == self.END_MARKER:
                                    # Parse the data
                                    try:
                                        fmt = f"<{self.N//2}f"
                                        self.fft_values = struct.unpack(fmt, self.buffer)
                                    except struct.error as e:
                                        print(f"Error unpacking data: {e}")
                                state = SEARCHING_START
                                
            except Exception as e:
                print(f"Error reading UART: {e}")
                state = SEARCHING_START

    def _update_plot(self, frame):
        self.ax.clear()
        
        # Scale FFT values using log10 for better visualization
        scaled_fft = np.log10(np.array(self.fft_values) + 1)  # Add 1 to avoid log(0)
        
        # Find peak frequency
        max_idx = np.argmax(scaled_fft)
        max_freq = self.freq_range[max_idx]
        self.max_freq_points.append(max_freq)
        freq_avg = np.mean(self.max_freq_points)
        
        # Plot setup
        self.ax.set_title('Real-time FFT Analysis', color='white', pad=20)
        self.ax.set_xlabel('Frequency (Hz)', color='white')
        self.ax.set_ylabel('Magnitude (log scale)', color='white')
        self.ax.grid(True, alpha=0.3)
        
        # Set axis limits
        self.ax.set_xlim(0, self.sample_rate/2)
        self.ax.set_ylim(0, max(1, max(scaled_fft) * 1.2))
        
        # Plot FFT data
        self.ax.plot(self.freq_range, scaled_fft, 'c-', alpha=0.7, label='FFT')
        
        # Highlight peak
        self.ax.plot(max_freq, scaled_fft[max_idx], 'ro', markersize=8)
        self.ax.annotate(f'Peak: {max_freq:.1f} Hz\nMag: {self.fft_values[max_idx]:.1f}',
                        xy=(max_freq, scaled_fft[max_idx]),
                        xytext=(max_freq + self.sample_rate/12, scaled_fft[max_idx] * 0.9),
                        color='white',
                        arrowprops=dict(facecolor='white', shrink=0.05))
        
        # Show average peak frequency
        self.ax.axvline(x=freq_avg, color='r', linestyle='--', alpha=0.5,
                       label=f'Avg Peak: {freq_avg:.1f} Hz')
        
        self.ax.legend(loc='upper right')
        
        # Add frequency range indicators
        for freq in [1000, 5000, 10000, 15000, 20000]:
            self.ax.axvline(x=freq, color='gray', linestyle=':', alpha=0.2)
            self.ax.text(freq, 0, f'{freq/1000}kHz', alpha=0.5, color='white')

    def run(self):
        ani = FuncAnimation(self.fig, self._update_plot, 
                          cache_frame_data=False,  # Disable frame caching
                          interval=50)             # Update every 50ms
        plt.show()
        
    def close(self):
        self.running = False
        if hasattr(self, 'uart') and self.uart.is_open:
            self.uart.close()
        plt.close()

if __name__ == "__main__":
    try:
        plotter = FFTPlotter()
        plotter.run()
    except KeyboardInterrupt:
        print("\nClosing application...")
        plotter.close()
    except Exception as e:
        print(f"Error: {e}")
        try:
            plotter.close()
        except:
            pass

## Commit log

2025-02-10 WIP, writing driver library
2025-02-26 Schematic initial multipart
    [MCU.kicad_sch, Mic.kicad_sch, Motor.kicad_sch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]
2025-02-26 adding the parts library
    [BQ27441DRZT-G1A.step, MCU.kicad_sch, Mic.kicad_sch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]
2025-02-26 pcb updated
    [tuner time.kicad_pcb]
2025-02-26 Demo UI with buttons
2025-03-01 Updated power schematic :D
    [power.kicad_sch]
2025-03-01 Updated UI w/ new header for OLED and updated MCU w/ STM32F405 and SWD (also some code I accdientally modified on this branch)
    [MCU.kicad_sch, oled.kicad_sch]
2025-03-01 Last push before PCB
    [0679L2000-05.step, Mic.kicad_sch, USB.kicad_sch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]
2025-03-01 changed the MICs to JST headers
    [B6B-PH-K-S.step, Mic.kicad_sch, Motor.kicad_sch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]
2025-03-01 changed debouncing order, switches to jst, and array resistors
    [B2B-PH-K-S.step, ESD9B5.0ST5G.step, MCU.kicad_sch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]
2025-03-02 PCB changes before changing Seth's clock
    [B4B-XH-A.step, EXB-2HV102JV.step, MCU.kicad_sch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]
2025-03-02 Update before adding AGND for the power delivery
    [MCU.kicad_sch, Mic.kicad_sch, Motor.kicad_sch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]
2025-03-02 Initial placement draft
    [B2B-XH-A.step, EEE1AA101WR.step, EXB-38V681JV.step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]
2025-03-04 bringing back the PCB to Life
    [tuner time.kicad_pcb]
2025-03-04 adjusted placments
    [MCU.kicad_sch, Mic.kicad_sch, Motor.kicad_sch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]
2025-03-04 Main routes done, no power planes, no DRC
    [tuner time.kicad_pcb, tuner time.kicad_sch]
2025-03-09 Power Layout done
    [MCU.kicad_sch, oled.kicad_sch, power.kicad_sch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]
2025-03-10 before annonation reset
    [oled.kicad_sch, power.kicad_sch, tuner time.kicad_sch]
2025-03-10 pushing BOM
    [BOM_3_10.csv, MCU.kicad_sch, Mic.kicad_sch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]
2025-03-12 adding the libraries and the new bom for footprint
    [BOM_for_footprint_3_10.csv, Motor.kicad_sch, tuner time.kicad_pcb]
2025-03-12 adding the crystal
    [MCU.kicad_sch, Mic.kicad_sch, Motor.kicad_sch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]
2025-03-12 added the footprints
2025-03-13 before oscilator
    [MCU.kicad_sch, Mic.kicad_sch, Motor.kicad_sch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]
2025-03-13 add before moving to lab computer
    [tuner time-B_Cu.gbr, tuner time-B_Mask.gbr, tuner time-B_Paste.gbr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]
2025-03-13 added the oscilator
    [MCU.kicad_sch, Mic.kicad_sch, Motor.kicad_sch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]
2025-03-13 push for jtag fix
    [MCU.kicad_sch, Mic.kicad_sch, Motor.kicad_sch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]
2025-03-13 Updated debug connection on MCU
    [MCU.kicad_sch]
2025-03-14 before major move
    [MCU.kicad_sch, Motor.kicad_sch, USB.kicad_sch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]
2025-03-14 Placement done
    [MCU.kicad_sch, Motor.kicad_sch, oled.kicad_sch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]
2025-03-14 placment is done now I swear
    [tuner time.kicad_pcb]
2025-03-14 before DRC
    [MCU.kicad_sch, Motor.kicad_sch, oled.kicad_sch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]
2025-03-14 done no text before stiching via
    [MCU.kicad_sch, Motor.kicad_sch, power.kicad_sch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]
2025-03-14 routing done no silkscreen
    [Mic.kicad_sch, tuner time.kicad_pcb]
2025-03-15 PCB all Done no Dr.Walter Review
    [BOM_3_10.csv, BOM_for_footprint_3_10.csv, MCU.kicad_sch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]
2025-03-26 last PCB
    [BOM_3_26.csv, power.kicad_sch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]
2025-04-17 PCB final
    [BOM_3_26.csv]
2025-04-24 with max print
2025-04-24 FIXED BATTERY LSFG
2025-04-24 WIP button motor feedback loop

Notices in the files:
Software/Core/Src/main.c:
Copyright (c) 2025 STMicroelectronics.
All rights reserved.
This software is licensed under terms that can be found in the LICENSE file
